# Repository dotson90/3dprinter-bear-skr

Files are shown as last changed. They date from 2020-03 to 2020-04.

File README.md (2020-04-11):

# เครื่องพิมพ์สามมิติ Bear SKR V1
## บทนำ
เครื่องพิมพ์สามมิติ Bear SKR เป็นเครื่องพิมพ์สามมิติสำหรับผู้ที่สนใจสร้างเครื่องพิมพ์สามมิติที่มีโครงสร้างแข็งแรง เชื่อถือได้ ทำให้พิมพ์งานได้เร็วขึ้น มีความแม่นยำสูง และซ่อมบำรุงง่าย
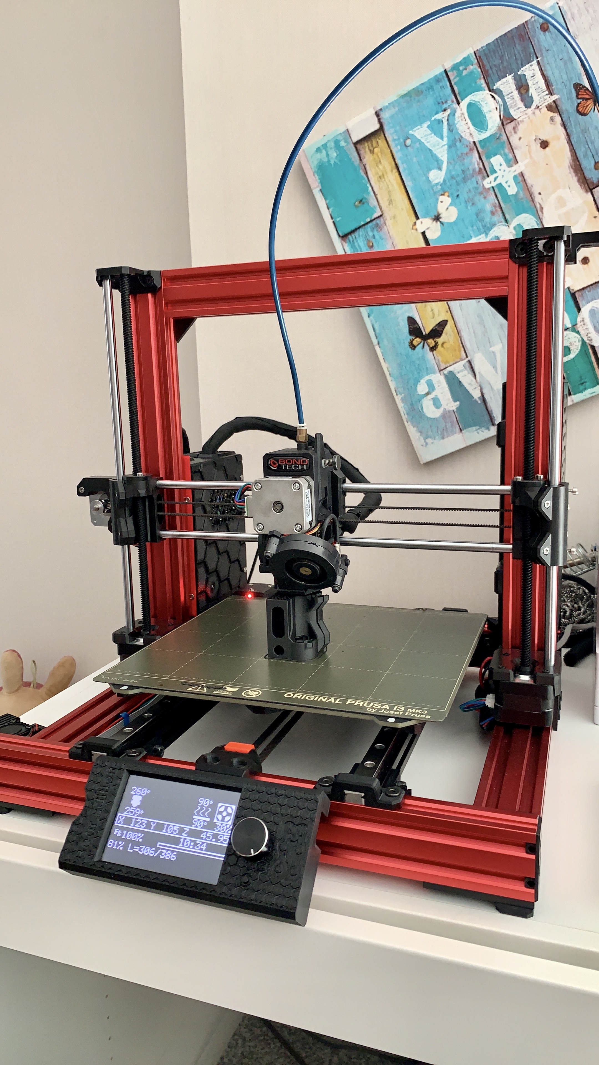
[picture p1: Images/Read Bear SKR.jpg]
Image description


## Todo
* 3D Printed Parts

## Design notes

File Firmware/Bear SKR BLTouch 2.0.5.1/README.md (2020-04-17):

# Bear SKR 2.0.5.1

* บอร์ต BigTreeTech SKR 1.4 Turbo
* BLTouch
* Bondtech BMG
* Stepper 1.8 @ 1A on X, Y, Z and E

### รายการที่แก้ไข

* Restore Flash as the default EEPROM emulation for LPC176x.
* Fix the Z_MIN_PROBE_PIN assignment on SKR 1.4.
* Fix progress bar and M73. (Update your Configuration_adv.h.)
* Fix U.B.L. slot loading.
* Fix Z correction after G29 (ABL Bilinear with Z Fade).
* Fix Z clearance move in G34.
* Fix "remaining time" cosmetic issue

### เปิดใช้ Feature ใหม่

* เปิดใช้งานตั้งฐานพิมพ์อัตโนมัติแบบ UBL

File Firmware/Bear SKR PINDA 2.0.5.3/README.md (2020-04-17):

# Bear SKR 2.0.5.3

### ใช้สำหรับ 

* บอร์ต BigTreeTech SKR 1.4 Turbo
* P.I.N.D.A
* Bondtech BMG
* Stepper 1.8 @ 1A on X, Y, Z and E

### New Features

* Add QSPI EEPROM for SAMD51.
* Case Light brightness stored in EEPROM.

### Issues Patched

* Fix Max7219 delay timing.
* Remove extra call to unskew.
* Formbot T-Rex 2+ default LCD timings.
* Fix M0 unused var warning.
* Fix stepper PWM menu.
* Float pins that can't pull down.
* Fix bad final M2/M3 Arc segment.

### Optimized / Improved

* Simplified SD completion.

### Configuration

* Allow PID_DEBUG to be turned on/off.

### Boards / Pins

* Funmat HT v4.0 board support.
* Fix up Trigorilla 1.4 pins.
* Fix FYSETC STM32 flash usage.
* Fix PINS_DEBUGGING build on STM32F1.

### Hosts and UI

* Update Russian and Italian languages.
* Fix SD finished ExtUI / host action.
* Limited backlash editing with Core kinematics.
* Fix / improve FTDI EVE Touch UI.

### เปิดใช้ Feature ใหม่

* เปิดใช้งานตั้งฐานพิมพ์อัตโนมัติแบบ UBL

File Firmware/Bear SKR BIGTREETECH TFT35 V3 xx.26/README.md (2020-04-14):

# Bear SKR TFT35 V3 xx.26

ใช้สำหรับ หน้าจอ BigTreeTech TFT35 V.3 เท่านั้น

มีการปรับปรุง และแก้ไขปัญหาต่าง ๆ ดังนี้

### เพิ่มเมนู

* เปลี่ยนหัวพิมพ์
* Calibration อัตโนมัติ
* Calibration สำหรับพิมพ์เส้น PLA
* Calibration สำหรับเส้น PETG
* ทำความสะอาดหัวพิมพ์ด้วยวิธีการ Cold Pull อัตโนมัติ
* เปิดให้ Feed เส้นในขนณะที่หัวพิมพ์เย็นได้
* ยกเลิกการ Feed เส้นในขฯะที่หัวพิมพ์เย็น
* Bed Level แบบ UBL อัตโนมัติ พร้อมทั้ง Save เข้า EEPROM Slot 1
* Bed Level แบบ UBL อัตโนมัติ พร้อมทั้ง Save เข้า EEPROM Slot 2
* Bed Level แบบ UBL อัตโนมัติ พร้อมทั้ง Save เข้า EEPROM Slot 3
* ตั้งระยะหัวพิมพ์แบบ UBL ขั้นตอนที่ 1
* ตั้งระยะหัวพิมพ์แบบ UBL ขั้นตอนที่ 2 พร้อมทั้ง Save เข้า EEPROM
* ทำการพิมพ์เพื่อทดสอบ Bed Level
* Adjust Point Near
* ล้าง EEPROM ไปเป็นค่าตั้งต้น

### New Features

* Add LCD backlight control, auto sleep function (Settings->Feature->LCD Brightness)
* Add more Printer setting parameters (Steps/mm, TMC driver current, Feedrate, Acceleration, etc...)
* Add new language(Polish, Slovak, Dutch, Hungarian), up to 15 languages are now supported
* Add support "M300" gcode for TFT buzzer
* Add the TFT with encoder can control the value of menu by encoder
* Add long file name display of onBoardSD(required LONG_FILENAME_HOST_SUPPORT in Marlin)

### Improve

* Improve print menu layout
* Improve Smart Filament Sensor(SFS), (note: required M114_DETAIL and disable LIN_ADVANCE in Marlin, because now LIN_ADVANCE have bugs in Marlin, will be fixed later)
* Improve the tips of "M117" and "echo:" from Marlin
* Improve power loss recovery(PLR), The printing state is saved per layer to reduce the wear of SD card(only support print from TFTSD card now).
* Improve model preview(only support print from TFTSD card now)
* Add more baudrate options on TFT screen

### Bugfix

* Fix error PS_ON_PIN from “PA12” to "PC12" in TFT35_V3.0
* Fix "M104","M109", 'R'/'B'/'F' parameters bug.

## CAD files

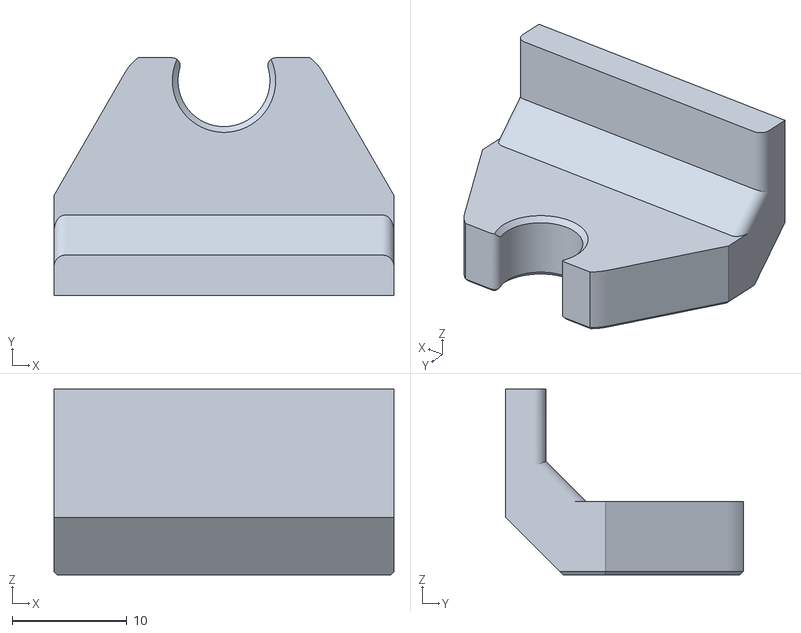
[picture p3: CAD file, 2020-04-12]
Printed Parts/Extruder/Hemera/y_axis_end_stop.stl
29.6 x 20.7 x 16.2

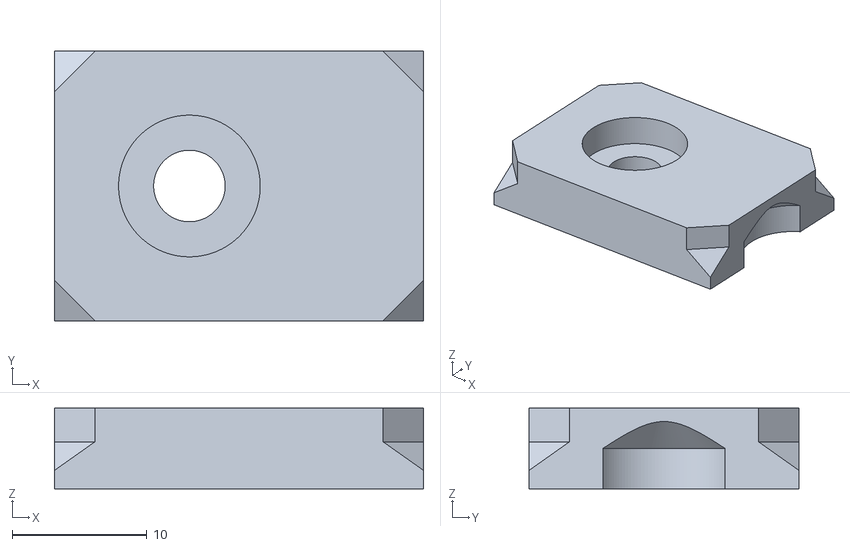
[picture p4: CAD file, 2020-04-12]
Printed Parts/Frame/Stl/foot.stl
27.4 x 20.0 x 6.00

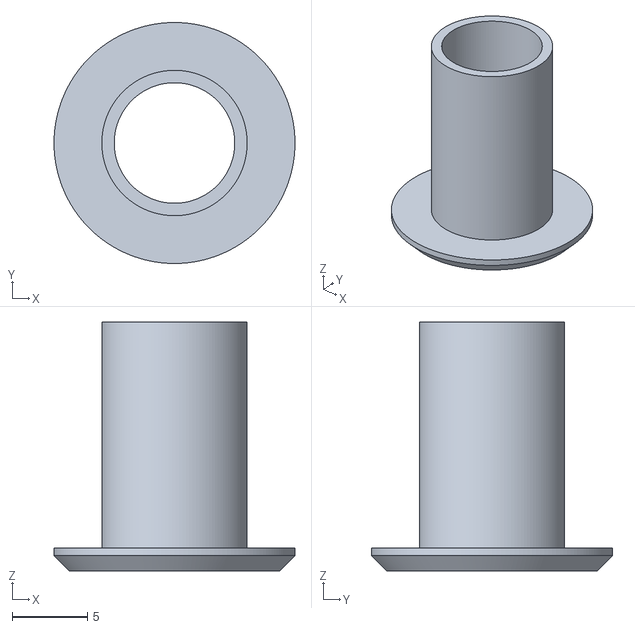
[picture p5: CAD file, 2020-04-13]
Printed Parts/Mean Well LRS-350 PSU Case/voltage_adjust_guide.stl
16.0 x 16.0 x 16.5

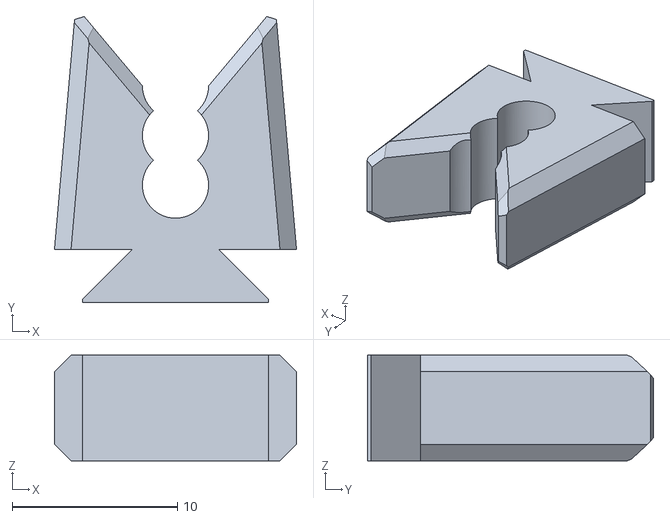
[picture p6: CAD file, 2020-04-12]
Printed Parts/SKR 1.4 Turbo Enclosure/Cable_Holder_Short.stl
14.6 x 17.3 x 6.40

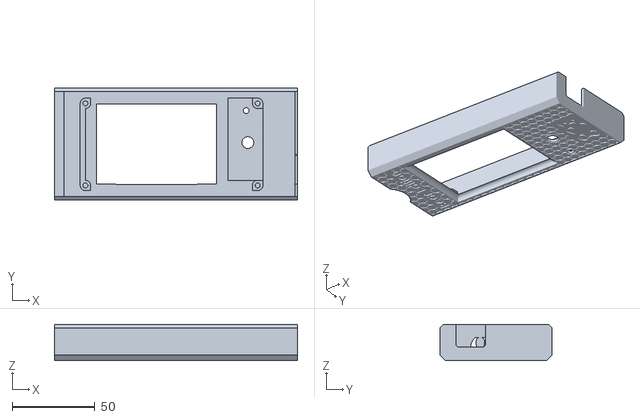
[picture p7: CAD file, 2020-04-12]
Printed Parts/TFT35 Bigtreetech LCD/cover_lcd_skr.stl
146.4 x 67.3 x 21.7

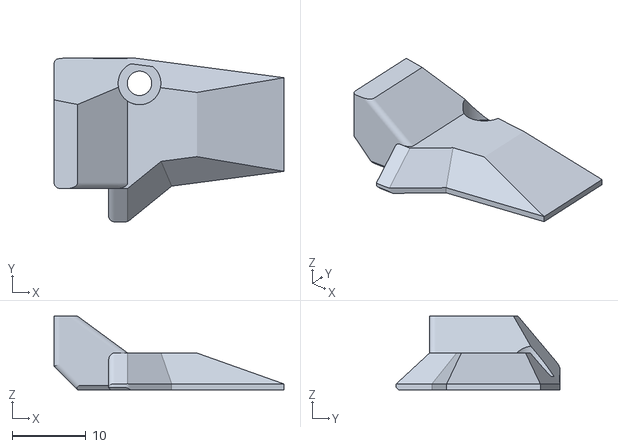
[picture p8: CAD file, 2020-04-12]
Printed Parts/Extruder/Hemera/cable_cover.stl
31.2 x 22.2 x 10.0

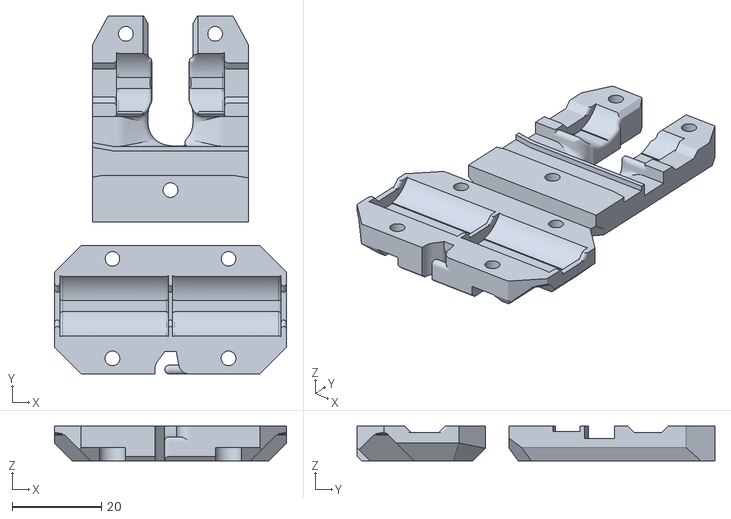
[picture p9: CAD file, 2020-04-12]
Printed Parts/Frame/Stl/x_carriage_back.stl
52.0 x 80.2 x 7.80

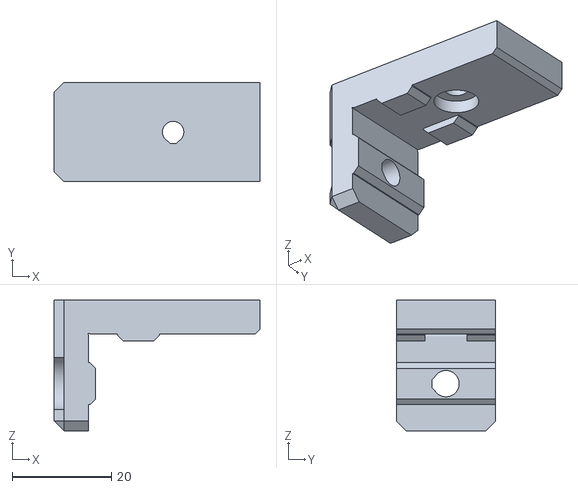
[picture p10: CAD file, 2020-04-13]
Printed Parts/Mean Well LRS-350 PSU Case/psu_upper_mount_mean_well_lrs_350.stl
41.5 x 20.0 x 26.3

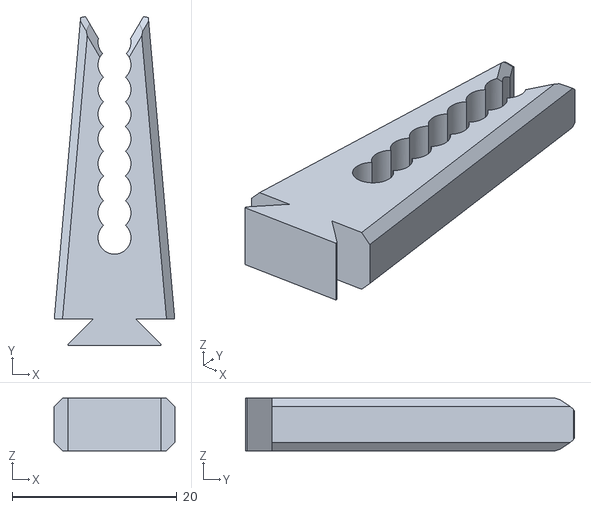
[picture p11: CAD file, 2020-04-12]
Printed Parts/SKR 1.4 Turbo Enclosure/Cable_Holder.stl
14.6 x 40.0 x 6.40

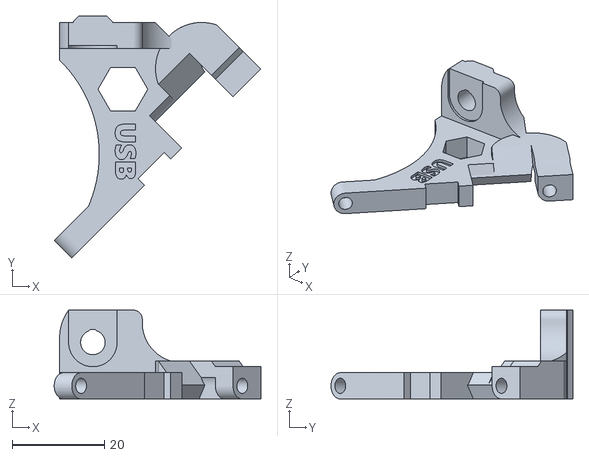
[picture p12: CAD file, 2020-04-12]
Printed Parts/TFT35 Bigtreetech LCD/usb_bracket.stl
44.8 x 52.5 x 19.3

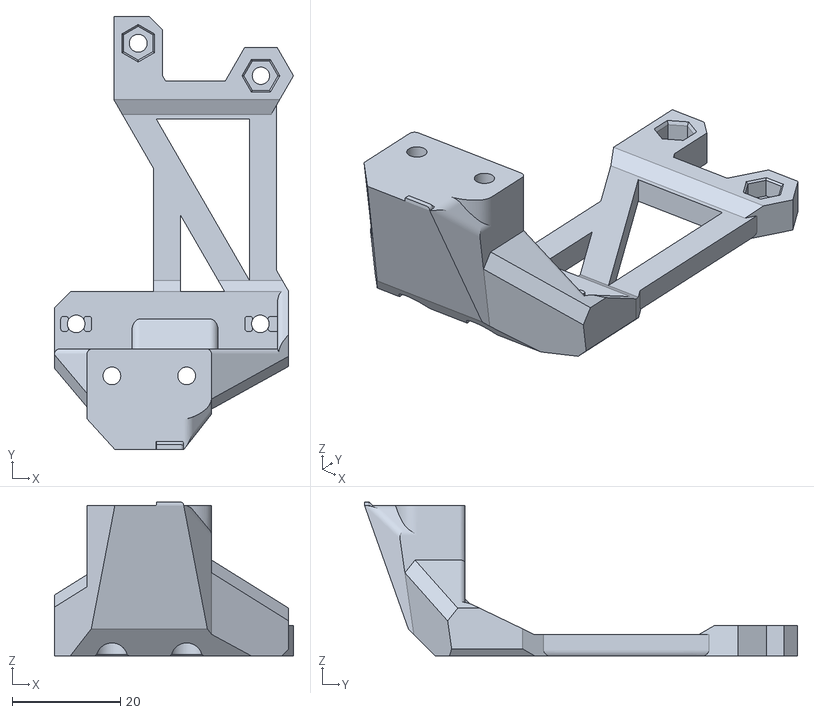
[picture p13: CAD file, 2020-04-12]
Printed Parts/Extruder/Hemera/body_front.stl
44.1 x 80.0 x 28.4

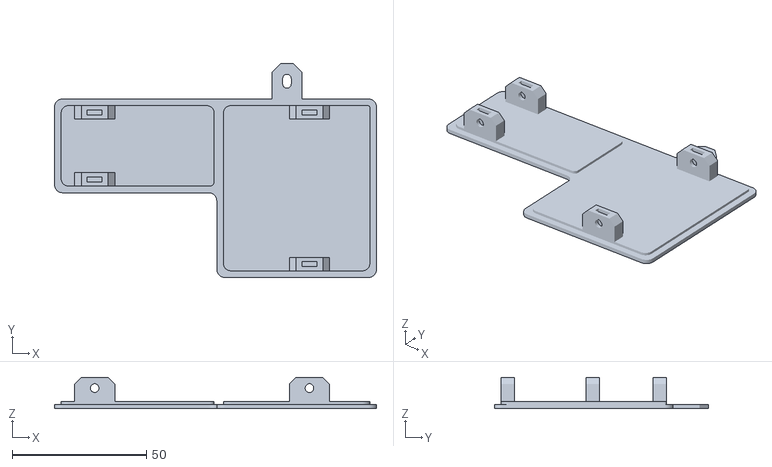
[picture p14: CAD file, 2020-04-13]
Printed Parts/Mean Well LRS-350 PSU Case/bottom.stl
119.9 x 79.7 x 11.6

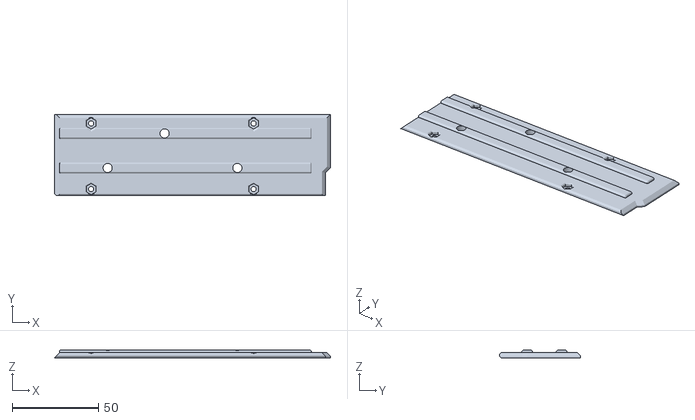
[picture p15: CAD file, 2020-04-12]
Printed Parts/SKR 1.4 Turbo Enclosure/Anchor_SKR_Bear_Short_1.stl
159.7 x 47.0 x 4.40

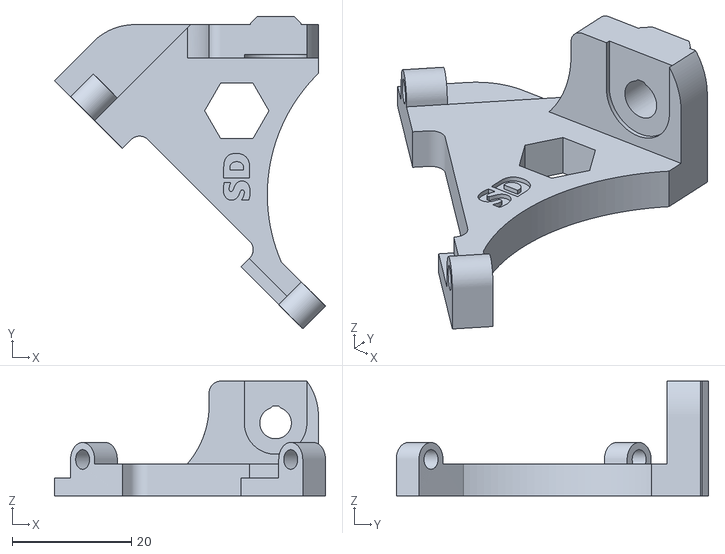
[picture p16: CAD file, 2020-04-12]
Printed Parts/TFT35 Bigtreetech LCD/sd_bracket.stl
45.5 x 52.5 x 19.3

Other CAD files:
Printed Parts/Extruder/Hemera/body_back.stl
Printed Parts/Frame/Stl/y_idler_tensioner_e3d.stl
Printed Parts/Mean Well LRS-350 PSU Case/case.stl
Printed Parts/SKR 1.4 Turbo Enclosure/ESP8266_Cover.stl
Printed Parts/Extruder/Hemera/nozzle_fan_duct.stl
Printed Parts/Extruder/Hemera/nozzle_fan_spacer.stl
Printed Parts/Extruder/Hemera/pinda_mount.stl
Printed Parts/Extruder/Hemera/ptfe_collet_clip.stl
Printed Parts/Extruder/Hemera/x_carriage.stl
Printed Parts/Frame/Stl/bondtech_x_carriage_mk3s.stl
Printed Parts/Frame/Stl/build_helper_y.stl
Printed Parts/Frame/Stl/build_helper_z.stl
Printed Parts/Frame/Stl/cable_clip_lcd.stl
Printed Parts/Frame/Stl/cable_clip_vertical.stl
Printed Parts/Frame/Stl/cable_guide_back_a.stl
Printed Parts/Frame/Stl/cable_guide_back_b.stl
Printed Parts/Frame/Stl/vslot_mount_pc4-m10.stl
Printed Parts/Frame/Stl/x_end_idler.stl
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

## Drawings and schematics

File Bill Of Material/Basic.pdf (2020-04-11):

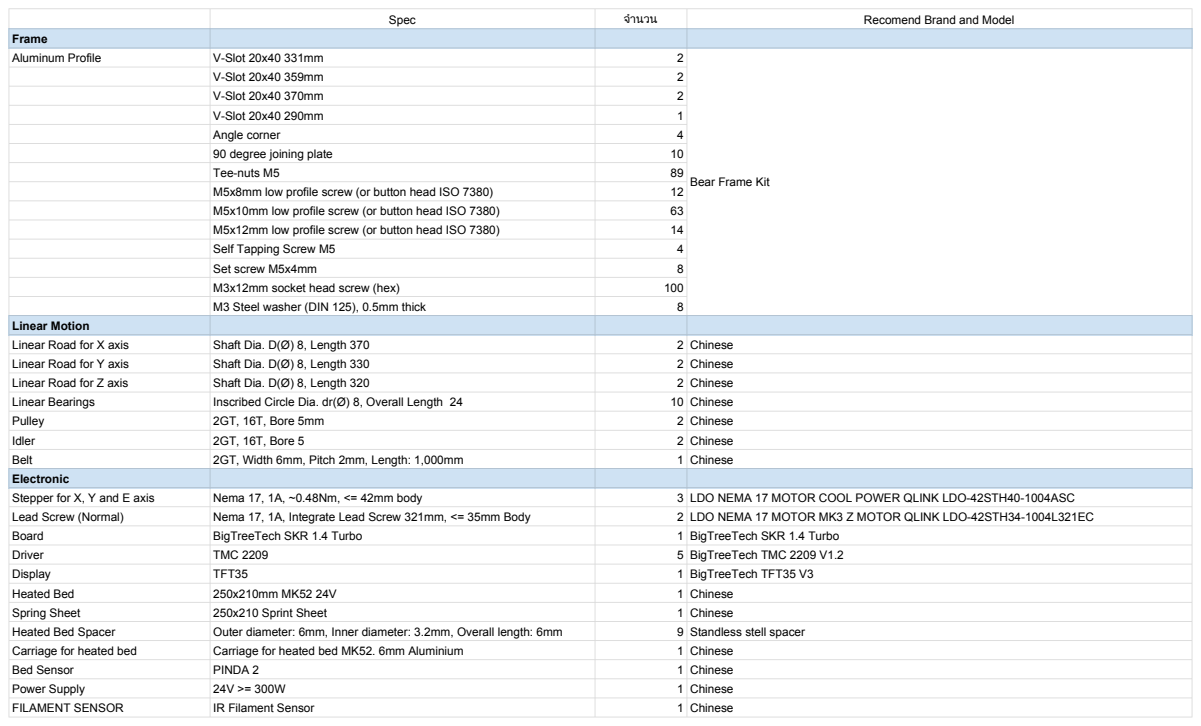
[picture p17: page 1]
Spec; จำนวน; Recomend Brand and Model; Frame; Aluminum Profile; V-Slot 20x40 331mm; V-Slot 20x40 359mm; V-Slot 20x40 370mm; V-Slot 20x40 290mm; Angle corner; 90 degree joining plate; Tee-nuts M5; M5x8mm low profile screw (or button head ISO 7380); M5x10mm low profile screw (or button head ISO 7380); M5x12mm low profile screw (or button head ISO 7380); Self Tapping Screw M5; Set screw M5x4mm; M3x12mm socket head screw (hex); M3 Steel washer (DIN 125), 0.5mm thick; Linear Motion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

Bear Frame Kit

Other | อุปกรณอื่น ๆ เชนสายไฟ ปลั๊ก นอต สกลู M3 | | Chinese หรือ บานหมอ

Extruders
Hotend | E3D V6 | 1 | Clone E3D V6 24V
Drive Gear | BondTech Drivegear KIT 1.75 Inner 5.0 | 1 | Clone BondTech Drivegear KIT 1.75 Inner 5.0
Extruder springs | d = 0.8mm, D = 5.0mm, L = 15.0mm, n = 10, Lm = 8.8mm, Fm = 41.08N | 1 | Original Prusa Extruder Springs
Extruder Fan | 4010 24V | 1 | Chinese
Printed Fan | Radial Cooling Fan 5015 24V | 1 | Chinese

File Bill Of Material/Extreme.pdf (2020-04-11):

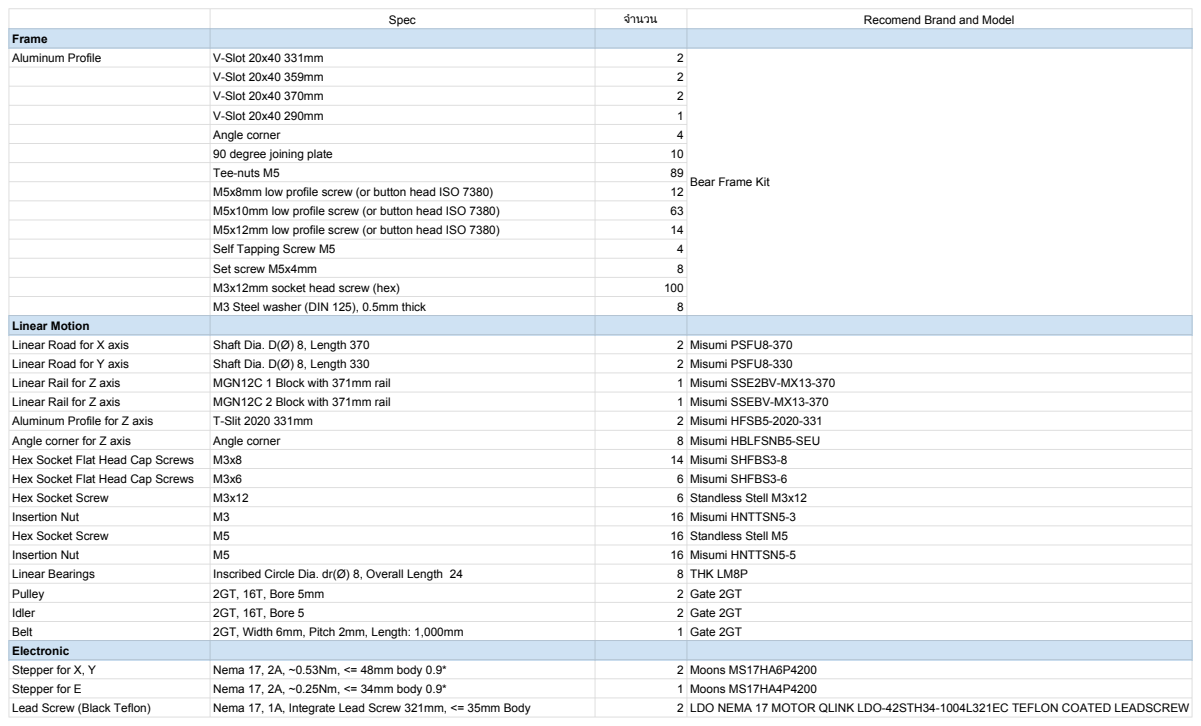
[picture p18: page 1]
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

Bear Frame Kit

Board | BigTreeTech SKR 1.4 Turbo | 1 | BigTreeTech SKR 1.4 Turbo
Driver | TMC 2209 | 5 | BigTreeTech TMC 2209 V1.2
Display | TFT35 | 1 | BigTreeTech TFT35 V3
Heated Bed | MK52 24V | 1 | LDO MK52 24V หรือ Originl Prusa MK52 24V
Heated Bed Spacer | Outer diameter: 6mm, Inner diameter: 3.2mm, Overall length: 6mm | 9 | Standless stell spacer
Carriage for heated bed | Carriage for heated bed MK52. 6mm Aluminium | 1 | Original Prusa Carriage for MK3
Bed Sensor | PINDA 2 | 1 | Original Prusa PINDA 2
Power Supply | 24V >= 300W | 1 | Mean Well LRS-350-24
FILAMENT SENSOR | IR Filament Sensor | 1 | Original Prusa MK3S IR FILAMENT SENSOR
Other | อุปกรณอื่น ๆ เชนสายไฟ ปลั๊ก นอต สกลู M3

Extruders
Hotend | Mosquito Hotend | 1 | Slicer Engineering Mosquito Hotend 24V
Bondtech Extruder upgrade | Prusa I3 MK3S Extruder Mosquito upgrade | 1 | Bondtech Prusa I3 MK3S Extruder Mosquito upgrade
Extruder Fan | 4010 24V | 1 | Mechatronic G4010L24B
Printed Fan | Radial Cooling Fan 5015 24V | 1 | Sanyo Denki 109BC24GC7-1

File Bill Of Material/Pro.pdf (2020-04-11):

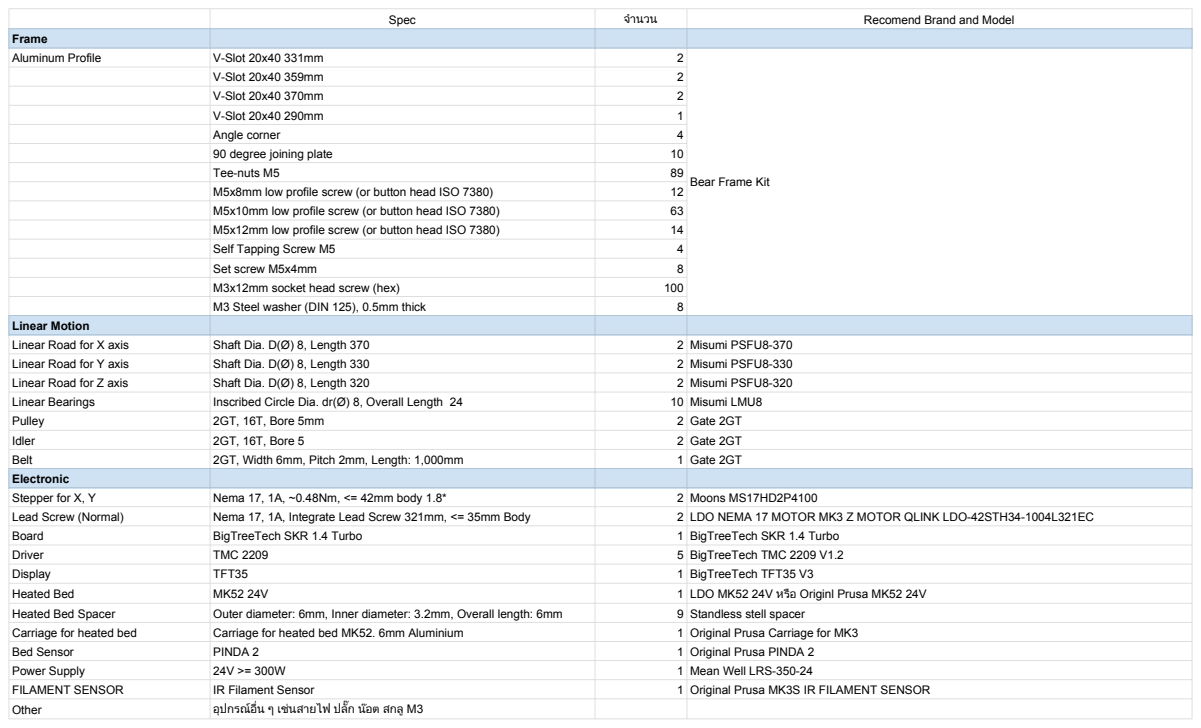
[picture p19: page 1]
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

Bear Frame Kit

Extruders
Hotend | E3D V6 | 1 | E3D V6 24V (Kit)
Bondtech Extruder upgrade | Prusa I3 MK3S Extruder upgrade | 1 | Bondtech Prusa I3 MK3S Extruder upgrade
Extruder Fan | 4010 24V | 1 | SUNON 4010 24V
Printed Fan | Radial Cooling Fan 5015 24V | 1 | SUNON 5015 24V

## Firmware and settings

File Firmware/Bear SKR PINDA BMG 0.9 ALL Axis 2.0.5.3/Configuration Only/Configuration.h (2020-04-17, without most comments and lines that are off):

#pragma once
#define CONFIGURATION_H_VERSION 020005
#define STRING_CONFIG_H_AUTHOR "(Narasak Mansurang, SKR V1.4 Turbo Bear BMG/TMC2209/PINDA)" // Who made the changes.
#define SHOW_BOOTSCREEN
#define SERIAL_PORT 0
#define SERIAL_PORT_2 -1
#define BAUDRATE 115200
  #define MOTHERBOARD BOARD_BTT_SKR_V1_4_TURBO
#define CUSTOM_MACHINE_NAME "Read Bear SKR Turbo"
#define EXTRUDERS 1
#define DEFAULT_NOMINAL_FILAMENT_DIA 1.75
#define TEMP_SENSOR_0 5
#define TEMP_SENSOR_1 0
#define TEMP_SENSOR_2 0
#define TEMP_SENSOR_3 0
#define TEMP_SENSOR_4 0
#define TEMP_SENSOR_5 0
#define TEMP_SENSOR_6 0
#define TEMP_SENSOR_7 0
#define TEMP_SENSOR_BED 1
#define TEMP_SENSOR_PROBE 1
#define TEMP_SENSOR_CHAMBER 0
#define DUMMY_THERMISTOR_998_VALUE 25
#define DUMMY_THERMISTOR_999_VALUE 100
#define MAX_REDUNDANT_TEMP_SENSOR_DIFF 10
#define TEMP_RESIDENCY_TIME     10  // (seconds) Time to wait for hotend to "settle" in M109
#define TEMP_WINDOW              3  // (°C) Temperature proximity for the "temperature reached" timer
#define TEMP_HYSTERESIS          8  // (°C) Temperature proximity considered "close enough" to the target
#define TEMP_BED_RESIDENCY_TIME 10  // (seconds) Time to wait for bed to "settle" in M190
#define TEMP_BED_WINDOW          3  // (°C) Temperature proximity for the "temperature reached" timer
#define TEMP_BED_HYSTERESIS      8  // (°C) Temperature proximity considered "close enough" to the target
#define HEATER_0_MINTEMP   5
#define HEATER_1_MINTEMP   5
#define HEATER_2_MINTEMP   5
#define HEATER_3_MINTEMP   5
#define HEATER_4_MINTEMP   5
#define HEATER_5_MINTEMP   5
#define HEATER_6_MINTEMP   5
#define HEATER_7_MINTEMP   5
#define BED_MINTEMP        5
#define HEATER_0_MAXTEMP 295
#define HEATER_1_MAXTEMP 275
#define HEATER_2_MAXTEMP 275
#define HEATER_3_MAXTEMP 275
#define HEATER_4_MAXTEMP 275
#define HEATER_5_MAXTEMP 275
#define HEATER_6_MAXTEMP 275
#define HEATER_7_MAXTEMP 275
#define BED_MAXTEMP      120
#define PIDTEMP
#define BANG_MAX 255     // Limits current to nozzle while in bang-bang mode; 255=full current
#define PID_MAX BANG_MAX // Limits current to nozzle while PID is active (see PID_FUNCTIONAL_RANGE below); 255=full current
#define PID_K1 0.95      // Smoothing factor within any PID loop
  #define PID_AUTOTUNE_MENU     // Add PID auto-tuning to the "Advanced Settings" menu. (~250 bytes of PROGMEM)
  #define PID_FUNCTIONAL_RANGE 10 // If the temperature difference between the target temperature and the actual temperature
  #define DEFAULT_Kp 16.13
  #define DEFAULT_Ki 1.16
  #define DEFAULT_Kd 56.23
#define PIDTEMPBED
#define MAX_BED_POWER 255 // limits duty cycle to bed; 255=full current
  #define DEFAULT_bedKp 126.13
  #define DEFAULT_bedKi 4.30
  #define DEFAULT_bedKd 924.76
#define PREVENT_COLD_EXTRUSION
#define EXTRUDE_MINTEMP 180
#define PREVENT_LENGTHY_EXTRUDE
#define EXTRUDE_MAXLENGTH 200
#define THERMAL_PROTECTION_HOTENDS // Enable thermal protection for all extruders
#define THERMAL_PROTECTION_BED     // Enable thermal protection for the heated bed
#define THERMAL_PROTECTION_CHAMBER // Enable thermal protection for the heated chamber
#define USE_XMIN_PLUG
#define USE_YMIN_PLUG
#define USE_ZMIN_PLUG
#define ENDSTOPPULLUPS
#define X_MIN_ENDSTOP_INVERTING false // Set to true to invert the logic of the endstop.
#define Y_MIN_ENDSTOP_INVERTING false // Set to true to invert the logic of the endstop.
#define Z_MIN_ENDSTOP_INVERTING false // Set to true to invert the logic of the endstop.
#define X_MAX_ENDSTOP_INVERTING false // Set to true to invert the logic of the endstop.
#define Y_MAX_ENDSTOP_INVERTING false // Set to true to invert the logic of the endstop.
#define Z_MAX_ENDSTOP_INVERTING false // Set to true to invert the logic of the endstop.
#define Z_MIN_PROBE_ENDSTOP_INVERTING false // Set to true to invert the logic of the probe.
#define X_DRIVER_TYPE  TMC2209
#define Y_DRIVER_TYPE  TMC2209
#define Z_DRIVER_TYPE  TMC2209
#define Z2_DRIVER_TYPE TMC2209
#define E0_DRIVER_TYPE TMC2209
#define DEFAULT_AXIS_STEPS_PER_UNIT   { 400, 400, 400, 1660 }
#define DEFAULT_MAX_FEEDRATE          { 200, 200, 30, 120 }
#define DEFAULT_MAX_ACCELERATION      { 1250, 1250, 200, 10000 }
#define DEFAULT_ACCELERATION          1250    // X, Y, Z and E acceleration for printing moves
#define DEFAULT_RETRACT_ACCELERATION  1250    // E acceleration for retracts
#define DEFAULT_TRAVEL_ACCELERATION   1250   // X, Y, Z acceleration for travel (non printing) moves
#define DEFAULT_EJERK    3.5  // May be used by Linear Advance
  #define JUNCTION_DEVIATION_MM 0.017 // (mm) Distance from real junction edge
#define S_CURVE_ACCELERATION
#define Z_MIN_PROBE_USES_Z_MIN_ENDSTOP_PIN
#define FIX_MOUNTED_PROBE
#define NOZZLE_TO_PROBE_OFFSET { 23, 5, 0 }
#define MIN_PROBE_EDGE 10
#define XY_PROBE_SPEED 8000
#define Z_PROBE_SPEED_FAST (HOMING_FEEDRATE_Z * 4)
#define Z_PROBE_SPEED_SLOW (Z_PROBE_SPEED_FAST / 2)
#define MULTIPLE_PROBING 3
#define Z_CLEARANCE_DEPLOY_PROBE    2 // Z Clearance for Deploy/Stow
#define Z_CLEARANCE_BETWEEN_PROBES  2 // Z Clearance between probe points
#define Z_CLEARANCE_MULTI_PROBE     2 // Z Clearance between multiple probes
#define Z_PROBE_LOW_POINT          -2 // Farthest distance below the trigger-point to go before stopping
#define Z_PROBE_OFFSET_RANGE_MIN -20
#define Z_PROBE_OFFSET_RANGE_MAX 20
#define Z_MIN_PROBE_REPEATABILITY_TEST
#define X_ENABLE_ON 0
#define Y_ENABLE_ON 0
#define Z_ENABLE_ON 0
#define E_ENABLE_ON 0 // For all extruders
#define DISABLE_X false
#define DISABLE_Y false
#define DISABLE_Z false
#define DISABLE_E false             // For all extruders
#define DISABLE_INACTIVE_EXTRUDER   // Keep only the active extruder enabled
#define INVERT_X_DIR false
#define INVERT_Y_DIR true
#define INVERT_Z_DIR false
#define INVERT_E0_DIR false
#define INVERT_E1_DIR false
#define INVERT_E2_DIR false
#define INVERT_E3_DIR false
#define INVERT_E4_DIR false
#define INVERT_E5_DIR false
#define INVERT_E6_DIR false
#define INVERT_E7_DIR false
#define X_HOME_DIR -1
#define Y_HOME_DIR -1
#define Z_HOME_DIR -1
#define X_BED_SIZE 250
#define Y_BED_SIZE 212.5
#define X_MIN_POS 0
#define Y_MIN_POS -4
#define Z_MIN_POS 0
#define X_MAX_POS X_BED_SIZE
#define Y_MAX_POS Y_BED_SIZE
#define Z_MAX_POS 210
#define MIN_SOFTWARE_ENDSTOPS
  #define MIN_SOFTWARE_ENDSTOP_X
  #define MIN_SOFTWARE_ENDSTOP_Y
  #define MIN_SOFTWARE_ENDSTOP_Z
#define MAX_SOFTWARE_ENDSTOPS
  #define MAX_SOFTWARE_ENDSTOP_X
  #define MAX_SOFTWARE_ENDSTOP_Y
  #define MAX_SOFTWARE_ENDSTOP_Z
  #define SOFT_ENDSTOPS_MENU_ITEM  // Enable/Disable software endstops from the LCD
#define FILAMENT_RUNOUT_SENSOR
  #define NUM_RUNOUT_SENSORS   1     // Number of sensors, up to one per extruder. Define a FIL_RUNOUT#_PIN for each.
  #define FIL_RUNOUT_INVERTING true // Set to true to invert the logic of the sensor.
  #define FIL_RUNOUT_PULLUP          // Use internal pullup for filament runout pins.
  #define FILAMENT_RUNOUT_SCRIPT "M600"
  #define FILAMENT_RUNOUT_DISTANCE_MM 2
#define AUTO_BED_LEVELING_UBL
#define RESTORE_LEVELING_AFTER_G28
  #define ENABLE_LEVELING_FADE_HEIGHT
  #define SEGMENT_LEVELED_MOVES
  #define LEVELED_SEGMENT_LENGTH 5.0 // (mm) Length of all segments (except the last one)
  #define G26_MESH_VALIDATION
    #define MESH_TEST_NOZZLE_SIZE    0.4  // (mm) Diameter of primary nozzle.
    #define MESH_TEST_LAYER_HEIGHT   0.2  // (mm) Default layer height for the G26 Mesh Validation Tool.
    #define MESH_TEST_HOTEND_TEMP  210    // (°C) Default nozzle temperature for the G26 Mesh Validation Tool.
    #define MESH_TEST_BED_TEMP      60    // (°C) Default bed temperature for the G26 Mesh Validation Tool.
    #define G26_XY_FEEDRATE         20    // (mm/s) Feedrate for XY Moves for the G26 Mesh Validation Tool.
    #define G26_RETRACT_MULTIPLIER   1.0  // G26 Q (retraction) used by default between mesh test elements.
  #define MESH_INSET 1              // Set Mesh bounds as an inset region of the bed
  #define GRID_MAX_POINTS_X 10       // Don't use more than 15 points per axis, implementation limited.
  #define GRID_MAX_POINTS_Y GRID_MAX_POINTS_X
  #define UBL_MESH_EDIT_MOVES_Z     // Sophisticated users prefer no movement of nozzle
  #define UBL_SAVE_ACTIVE_ON_M500   // Save the currently active mesh in the current slot on M500
  #define UBL_Z_RAISE_WHEN_OFF_MESH 0 // When the nozzle is off the mesh, this value is used
#define MANUAL_X_HOME_POS 0
#define MANUAL_Y_HOME_POS -3
#define MANUAL_Z_HOME_POS 0.2
#define Z_SAFE_HOMING
  #define Z_SAFE_HOMING_X_POINT ((X_BED_SIZE) / 2)    // X point for Z homing when homing all axes (G28).
  #define Z_SAFE_HOMING_Y_POINT ((Y_BED_SIZE) / 2)    // Y point for Z homing when homing all axes (G28).
#define HOMING_FEEDRATE_XY (50*60)
#define HOMING_FEEDRATE_Z  (4*60)
#define VALIDATE_HOMING_ENDSTOPS
#define EEPROM_SETTINGS     // Persistent storage with M500 and M501
#define EEPROM_CHITCHAT       // Give feedback on EEPROM commands. Disable to save PROGMEM.
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

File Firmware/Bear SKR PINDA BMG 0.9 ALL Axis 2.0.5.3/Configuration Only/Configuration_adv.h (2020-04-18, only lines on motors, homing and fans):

#define E0_AUTO_FAN_PIN P2_04
#define E1_AUTO_FAN_PIN -1
#define E2_AUTO_FAN_PIN -1
#define E3_AUTO_FAN_PIN -1
#define E4_AUTO_FAN_PIN -1
#define E5_AUTO_FAN_PIN -1
#define CHAMBER_AUTO_FAN_PIN -1
#define X_HOME_BUMP_MM 0
#define Y_HOME_BUMP_MM 0
#define Z_HOME_BUMP_MM 0
#define HOMING_BUMP_DIVISOR { 2, 2, 4 }  // Re-Bump Speed Divisor (Divides the Homing Feedrate)
#define HOMING_BACKOFF_MM { 2, 2, 2 }  // (mm) Move away from the endstops after homing
  #define HOME_AFTER_G34
#define MICROSTEP_MODES { 16, 16, 16, 16, 16, 16 } // [1,2,4,8,16]
#define DIGIPOT_I2C_MOTOR_CURRENTS { 1.0, 1.0, 1.0, 1.0, 1.0, 1.0, 1.0, 1.0 }  //  AZTEEG_X3_PRO
#define LIN_ADVANCE
  #define LIN_ADVANCE_K 0.00    // Unit: mm compression per 1mm/s extruder speed
#define ADVANCED_PAUSE_FEATURE
  #define ADVANCED_PAUSE_PURGE_FEEDRATE        3  // (mm/s) Extrude feedrate (after loading). Should be slower than load feedrate.
  #define ADVANCED_PAUSE_PURGE_LENGTH         60  // (mm) Length to extrude after loading.
  #define ADVANCED_PAUSE_RESUME_PRIME          0  // (mm) Extra distance to prime nozzle after returning from park.
    #define X_CURRENT       1400        // (mA) RMS current. Multiply by 1.414 for peak current.
    #define X_CURRENT_HOME  300  // (mA) RMS current for sensorless homing
    #define X_MICROSTEPS     32    // 0..256
    #define Y_CURRENT       1400
    #define Y_CURRENT_HOME  400
    #define Y_MICROSTEPS     32
    #define Z_CURRENT       450
    #define Z_CURRENT_HOME  Z_CURRENT
    #define Z_MICROSTEPS     16
    #define Z2_CURRENT      450
    #define Z2_CURRENT_HOME Z2_CURRENT
    #define Z2_MICROSTEPS    16
    #define E0_CURRENT      1400
    #define E0_MICROSTEPS    32
    #define CURRENT_STEP_DOWN     50  // [mA]
    #define REPORT_CURRENT_CHANGE
  #define X_HYBRID_THRESHOLD     100  // [mm/s]
  #define X2_HYBRID_THRESHOLD    100
  #define Y_HYBRID_THRESHOLD     100
  #define Y2_HYBRID_THRESHOLD    100
  #define Z_HYBRID_THRESHOLD       3
  #define Z2_HYBRID_THRESHOLD      3
  #define Z3_HYBRID_THRESHOLD      3
  #define Z4_HYBRID_THRESHOLD      3
  #define E0_HYBRID_THRESHOLD     30
  #define E1_HYBRID_THRESHOLD     30
  #define E2_HYBRID_THRESHOLD     30
  #define E3_HYBRID_THRESHOLD     30
  #define E4_HYBRID_THRESHOLD     30
  #define E5_HYBRID_THRESHOLD     30
  #define E6_HYBRID_THRESHOLD     30
  #define E7_HYBRID_THRESHOLD     30
  #define SENSORLESS_HOMING // StallGuard capable drivers only
    #define X_STALL_SENSITIVITY  81
    #define X2_STALL_SENSITIVITY X_STALL_SENSITIVITY
    #define Y_STALL_SENSITIVITY  85
    #define IMPROVE_HOMING_RELIABILITY

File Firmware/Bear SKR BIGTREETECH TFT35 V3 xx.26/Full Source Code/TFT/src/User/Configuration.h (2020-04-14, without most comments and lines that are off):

#define _CONFIGRATION_H_
#define DEFAULT_LCD_MODE SERIAL_TSC
#define STARTUP_KNOB_LED_COLOR 1         // LED_OFF
#define KEEP_KNOB_LED_COLOR_MARLIN_MODE  // Keeps the LED state in Marlin Mode
#define DEFAULT_LCD_BRIGHTNESS      11  // 11: LCD_100_PERCENT - Brightness value from list
#define DEFAULT_LCD_IDLE_BRIGHTNESS 2   // 2: LCD_10_PERCENT - Brightness value from list
#define DEFAULT_LCD_IDLE_TIMER      1   // 1: LCD_DIM_OFF
#define LCD_DIM_CUSTOM_SECONDS      600 // Custom value in seconds. Will be used if
#define ST7920_BKCOLOR BLACK
#define ST7920_FNCOLOR YELLOW
#define DEFAULT_ST7920_FULLSCREEN_MODE 0 // 0: Disabled. RECOMMENDED FOR TFT24
#define BAUDRATE 115200
#define DEFAULT_LANGUAGE ENGLISH
#define SHOW_BTT_BOOTSCREEN
#define BUZZER_FREQUENCY_DURATION_MS 20 // Default 20
#define BUZZER_FREQUENCY_HZ 10000       // Default 10000, 20Hz to 60KHz
#define BUZZER_STOP_LEVEL false
#define TITLE_BACKGROUND_COLOR      BLACK  // Title background color // 0xD928
#define BACKGROUND_COLOR            BLACK  // Background color // 0x0A29
#define FONT_COLOR                  WHITE  // Font foreground color
#define REMINDER_FONT_COLOR         RED    // Reminder font color, such as: "No print attached", "Busy processing", etc.
#define VOLUME_REMINDER_FONT_COLOR  GBLUE  // Volume reminder font color, such as: "Card inserted", "Card removed"
#define TOOL_NUM     1    // set in 1~6
#define EXTRUDER_NUM 1    // set in 1~6
#define FAN_NUM      1    // set in 1~6
#define PREHEAT_BED      {60,      70,       100}
#define PREHEAT_HOTEND   {200,     250,      250}
#define HEAT_MAX_TEMP    {120,    295,       275,       275,       275,       275,       275}    //max temperature can be set
#define HEAT_SIGN_ID     {"B:",   "T0:",     "T1:",     "T2:",     "T3:",     "T4:",     "T5:"}
#define HEAT_DISPLAY_ID  {"Bed",  "T0",      "T1",      "T2",      "T3",      "T4",      "T5"}
#define HEAT_CMD         {"M140", "M104 T0", "M104 T1", "M104 T2", "M104 T3", "M104 T4", "M104 T5" };
#define HEAT_WAIT_CMD    {"M190", "M109 T0", "M109 T1", "M109 T2", "M109 T3", "M109 T4", "M109 T5" };
#define TOOL_CHANGE      {"T0",   "T1",      "T2",      "T3",      "T4",      "T5"}
#define EXTRUDER_ID      {"E0",   "E1",      "E2",      "E3",      "E4",      "E5"}
#define FAN_MAX_PWM      {255,       255,       255,       255,       255,       255}
#define FAN_ID           {"F0",    "F1",    "F2",    "F3",    "F4",    "F5"}
#define FAN_CMD          {"M106 P0", "M106 P1", "M106 P2", "M106 P3", "M106 P4", "M106 P5" };
#define SPEED_ID         {"Sp.", "Fr."}
#define AXIS_DISPLAY_ID  {"X",  "Y",  "Z",   "E",  "E2"}
#define DEFAULT_SPEED_MOVE      3000
#define SPEED_MOVE_SLOW         1000
#define SPEED_MOVE_FAST         5000
#define EXTRUDE_SLOW_SPEED      60
#define EXTRUDE_NORMAL_SPEED    600
#define EXTRUDE_FAST_SPEED      1200
#define X_MIN_POS 0
#define Y_MIN_POS -4
#define Z_MIN_POS 0
#define X_MAX_POS 250
#define Y_MAX_POS 212.5
#define Z_MAX_POS 210
#define NOZZLE_PAUSE_RETRACT_LENGTH 15   // (mm)
#define NOZZLE_RESUME_PURGE_LENGTH  16   // (mm)
#define NOZZLE_PAUSE_X_POSITION     (X_MIN_POS + 10)  // (mm) Must be an integer
#define NOZZLE_PAUSE_Y_POSITION     (Y_MIN_POS + 10)  // (mm) Must be an integer
#define NOZZLE_PAUSE_Z_RAISE        20   // (mm)
#define NOZZLE_PAUSE_E_FEEDRATE     6000 // (mm/min) retract & purge feedrate
#define NOZZLE_PAUSE_XY_FEEDRATE    6000 // (mm/min) X and Y axes feedrate
#define NOZZLE_PAUSE_Z_FEEDRATE     300  // (mm/min) Z axis feedrate
#define AUTO_SAVE_LOAD_LEVELING_VALUE
#define LEVELING_POINT_1_X         (X_MIN_POS + 20)
#define LEVELING_POINT_1_Y         (Y_MIN_POS + 20)
#define LEVELING_POINT_2_X         (X_MAX_POS - 20)
#define LEVELING_POINT_2_Y         (Y_MIN_POS + 20)
#define LEVELING_POINT_3_X         (X_MAX_POS - 20)
#define LEVELING_POINT_3_Y         (Y_MAX_POS - 20)
#define LEVELING_POINT_4_X         (X_MIN_POS + 20)
#define LEVELING_POINT_4_Y         (Y_MAX_POS - 20)
#define LEVELING_POINT_Z           0.2f  // Z-axis position when nozzle stays for leveling
#define LEVELING_POINT_MOVE_Z      10.0f // Z-axis position when nozzle move to next point
#define LEVELING_POINT_XY_FEEDRATE 6000  // (mm/min) X and Y axes move feedrate
#define LEVELING_POINT_Z_FEEDRATE  600   // (mm/min) Z axis move feedrate
#define PS_ON_ACTIVE_HIGH    true   // Set 'false' for ATX (1), 'true' for X-Box (2)
#define FIL_RUNOUT_INVERTING true  // Set to false to invert the logic of the sensor.
#define FIL_NOISE_THRESHOLD  100   // 100ms,  Pause print when filament runout is detected for 100ms.
#define FILAMENT_RUNOUT_DISTANCE_MM 7
#define ALTERNATIVE_MOVE_MENU
#define UNIFIED_MENU
#define ONBOARD_SD_SUPPORT
  #define M27_REFRESH                3        // Time in sec for M27 command
  #define M27_WATCH_OTHER_SOURCES    true     // if true the polling on M27 report is always active. Case: SD print started not from TFT35
#define POWER_LOSS_ZRAISE 10 // (mm) Raise Z axis on resume (on power loss with UPS)
#define PREVENT_COLD_EXTRUSION_MINTEMP 170
#define AUTO_SHUT_DOWN_MAXTEMP 50
#define SHOW_FAN_PERCENTAGE // enable to show fan speed as a percentage instead of a value
#define RAPID_SERIAL_COMM
#define CUSTOM_0_LABEL "Nozzle Change"
#define CUSTOM_0_GCODE "M104 S275\nM117 Setting Nozzle to 275C\nG4 s3\nM0 Click to continue"
#define CUSTOM_1_LABEL "Full Calibration"
#define CUSTOM_1_GCODE "M140 S60\nM190 S60\nG28\nG34\nG29\nM500\nM140 S0\nG28"
#define CUSTOM_2_LABEL "PLA Z Calibration"
#define CUSTOM_2_GCODE "G28\nM107\nM140 S60\nM190 S60\nM104 S160\nM109 S160\nG29 L1\nG1 X2.0 Y-2.0 Z0.60\nM104 S205\nM109 S205\nM0 Click to continue\nG92 E0.00\nG1 Z0.2 X60 E9.0 F1000.0\nG1 X100.0 E12.5 F1000.0\nG92 E0.0\nG21\nG90\nM83\nG1 E-1.50000 F2100.00000\nG1 Z0.150 F7200.000\nM204 S1000\nG1 F4000\nG1 X50 Y155\nG1 F1080\nG1 X75 Y155 E2.5\nG1 X100 Y155 E2\nG1 X200 Y155 E2.62773\nG1 X200 Y135 E0.66174\nG1 X50 Y135 E3.62773\nG1 X50 Y115 E0.49386\nG1 X200 Y115 E3.62773\nG1 X200 Y95 E0.49386\nG1 X50 Y95 E3.62773\nG1 X50 Y75 E0.49386\nG1 X200 Y75 E3.62773\nG1 X200 Y55 E0.49386\nG1 X50 Y55 E3.62773\nG1 X50 Y35 E0.49386\nG1 X70 Y35 E0.49386\nG1 X70 Y34.6 E0\nG1 X50 Y34.6 E0.49386\nG1 X50 Y34.2 E0\nG1 X70 Y34.2 E0.49386\nG1 X70 Y33.8 E0\nG1 X50 Y33.8 E0.49386\nG1 X50 Y33.4 E0\nG1 X70 Y33.4 E0.49386\nG1 X70 Y33.0 E0\nG1 X50 Y33.0 E0.49386\nG1 X50 Y32.6 E0\nG1 X70 Y32.6 E0.49386\nG1 X70 Y32.2 E0\nG1 X50 Y32.2 E0.49386\nG1 X50 Y31.8 E0\nG1 X70 Y31.8 E0.49386\nG1 X70 Y31.4 E0\nG1 X50 Y31.4 E0.49386\nG1 X50 Y31.0 E0\nG1 X70 Y31.0 E0.49386\nG1 X70 Y30.6 E0\nG1 X50 Y30.6 E0.49386\nG1 X50 Y30.2 E0\nG1 X70 Y30.2 E0.49386\nG1 X70 Y29.8 E0\nG1 X50 Y29.8 E0.49386\nG1 X50 Y29.4 E0\nG1 X70 Y29.4 E0.49386\nG1 X70 Y29.0 E0\nG1 X50 Y29.0 E0.49386\nG1 X50 Y28.6 E0\nG1 X70 Y28.6 E0.49386\nG1 X70 Y28.2 E0\nG1 X50 Y28.2 E0.49386\nG1 X50 Y27.8 E0\nG1 X70 Y27.8 E0.49386\nG1 X70 Y27.4 E0\nG1 X50 Y27.4 E0.49386\nG1 X50 Y27.0 E0\nG1 X70 Y27.0 E0.49386\nG1 X70 Y26.6 E0\nG1 X50 Y26.6 E0.49386\nG1 X50 Y26.2 E0\nG1 X70 Y26.2 E0.49386\nG1 X70 Y25.8 E0\nG1 X50 Y25.8 E0.49386\nG1 X50 Y25.4 E0\nG1 X70 Y25.4 E0.49386\nG1 X70 Y25.0 E0\nG1 X50 Y25.0 E0.49386\nG1 X50 Y24.6 E0\nG1 X70 Y24.6 E0.49386\nG1 X70 Y24.2 E0\nG1 X50 Y24.2 E0.49386\nG1 X50 Y23.8 E0\nG1 X70 Y23.8 E0.49386\nG1 X70 Y23.4 E0\nG1 X50 Y23.4 E0.49386\nG1 X50 Y23.0 E0\nG1 X70 Y23.0 E0.49386\nG1 X70 Y22.6 E0\nG1 X50 Y22.6 E0.49386\nG1 X50 Y22.2 E0\nG1 X70 Y22.2 E0.49386\nG1 X70 Y21.8 E0\nG1 X50 Y21.8 E0.49386\nG1 X50 Y21.4 E0\nG1 X70 Y21.4 E0.49386\nG1 X70 Y21.0 E0\nG1 X50 Y21.0 E0.49386\nG1 X50 Y20.6 E0\nG1 X70 Y20.6 E0.49386\nG1 X70 Y20.2 E0\nG1 X50 Y20.2 E0.49386\nG1 X50 Y19.8 E0\nG1 X70 Y19.8 E0.49386\nG1 X70 Y19.4 E0\nG1 X50 Y19.4 E0.49386\nG1 E-0.07500 F2100.00000\nG4\nM107\nM104 S0\nM140 S0\nG1 X10 Y180 F4000\nG1 Z10 F1300.000\nM500\nM0 Happy Printing\nM84"
#define CUSTOM_3_LABEL "PETG Z Calibration"
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

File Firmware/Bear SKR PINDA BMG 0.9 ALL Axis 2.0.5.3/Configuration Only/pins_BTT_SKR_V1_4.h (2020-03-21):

/**
 * Marlin 3D Printer Firmware
 * Copyright (c) 2020 MarlinFirmware [https://github.com/MarlinFirmware/Marlin]
 *
 * Based on Sprinter and grbl.
 * Copyright (c) 2011 Camiel Gubbels / Erik van der Zalm
 *
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
 */
#pragma once

#ifndef BOARD_INFO_NAME
  #define BOARD_INFO_NAME "BIGTREE SKR 1.4"
#endif

//
// EEPROM
//
#if NONE(FLASH_EEPROM_EMULATION, SDCARD_EEPROM_EMULATION)
  #define FLASH_EEPROM_EMULATION
  //#define SDCARD_EEPROM_EMULATION
#endif

//
// SD Connection
//
#ifndef SDCARD_CONNECTION
  #define SDCARD_CONNECTION LCD
#endif

//
// Servos
//
#define SERVO0_PIN         P2_00

//
// TMC StallGuard DIAG pins
//
#define X_DIAG_PIN         P1_29   // X-STOP
#define Y_DIAG_PIN         P1_28   // Y-STOP
#define Z_DIAG_PIN         P1_27   // Z-STOP
#define E0_DIAG_PIN        P1_26   // E0DET
#define E1_DIAG_PIN        P1_25   // E1DET

//
// Limit Switches
//
#if X_STALL_SENSITIVITY
  #define X_STOP_PIN       X_DIAG_PIN
  #if X_HOME_DIR < 0
    #define X_MAX_PIN      P1_26   // E0DET
  #else
    #define X_MIN_PIN      P1_26   // E0DET
  #endif
#else
  #define X_STOP_PIN       P1_29   // X-STOP
#endif

#if Y_STALL_SENSITIVITY
  #define Y_STOP_PIN       Y_DIAG_PIN
  #if Y_HOME_DIR < 0
    #define Y_MAX_PIN      P1_25   // E1DET
  #else
    #define Y_MIN_PIN      P1_25   // E1DET
  #endif
#else
  #define Y_STOP_PIN       P1_28   // Y-STOP
#endif

#if Z_STALL_SENSITIVITY
  #define Z_STOP_PIN       Z_DIAG_PIN
  #if Z_HOME_DIR < 0
    #define Z_MAX_PIN      P1_00   // PWRDET
  #else
    #define Z_MIN_PIN      P1_00   // PWRDET
  #endif
#else
  #ifndef Z_STOP_PIN
    #define Z_STOP_PIN     P0_10   // Z-STOP
  #endif
#endif

//
// Z Probe (when not Z_MIN_PIN)
//
#ifndef Z_MIN_PROBE_PIN
  #define Z_MIN_PROBE_PIN  P0_10
#endif

//
// Filament Runout Sensor
//
#define FIL_RUNOUT_PIN     P1_26   // E0DET
#define FIL_RUNOUT2_PIN    P1_25   // E1DET

//
// Power Supply Control
//
#ifndef PS_ON_PIN
  #define PS_ON_PIN        P1_00   // PWRDET
#endif

//
// Power Loss Detection
//
#ifndef POWER_LOSS_PIN
  #define POWER_LOSS_PIN   P1_00   // PWRDET
#endif

//
// Steppers
//
#define X_STEP_PIN         P2_02
#define X_DIR_PIN          P2_06
#define X_ENABLE_PIN       P2_01
#ifndef X_CS_PIN
  #define X_CS_PIN         P1_10
#endif

#define Y_STEP_PIN         P0_19
#define Y_DIR_PIN          P0_20
#define Y_ENABLE_PIN       P2_08
#ifndef Y_CS_PIN
  #define Y_CS_PIN         P1_09
#endif

#define Z_STEP_PIN         P0_22
#define Z_DIR_PIN          P2_11
#define Z_ENABLE_PIN       P0_21
#ifndef Z_CS_PIN
  #define Z_CS_PIN         P1_08
#endif

#define E0_STEP_PIN        P2_13
#define E0_DIR_PIN         P0_11
#define E0_ENABLE_PIN      P2_12
#ifndef E0_CS_PIN
  #define E0_CS_PIN        P1_04
#endif

#define E1_STEP_PIN        P1_15
#define E1_DIR_PIN         P1_14
#define E1_ENABLE_PIN      P1_16
#ifndef E1_CS_PIN
  #define E1_CS_PIN        P1_01
#endif

#define TEMP_1_PIN         P0_23_A0   // A2 (T2) - (69) - TEMP_1_PIN
#define TEMP_BED_PIN       P0_25_A2   // A0 (T0) - (67) - TEMP_BED_PIN

//
// Software SPI pins for TMC2130 stepper drivers
//
#if ENABLED(TMC_USE_SW_SPI)
  #ifndef TMC_SW_MOSI
    #define TMC_SW_MOSI    P1_17
  #endif
  #ifndef TMC_SW_MISO
    #define TMC_SW_MISO    P0_05
  #endif
  #ifndef TMC_SW_SCK
    #define TMC_SW_SCK     P0_04
  #endif
#endif

#if HAS_TMC220x
  /**
   * TMC2208/TMC2209 stepper drivers
   *
   * Hardware serial communication ports.
   * If undefined software serial is used according to the pins below
   */
  //#define X_HARDWARE_SERIAL  Serial
  //#define X2_HARDWARE_SERIAL Serial1
  //#define Y_HARDWARE_SERIAL  Serial1
  //#define Y2_HARDWARE_SERIAL Serial1
  //#define Z_HARDWARE_SERIAL  Serial1
  //#define Z2_HARDWARE_SERIAL Serial1
  //#define E0_HARDWARE_SERIAL Serial1
  //#define E1_HARDWARE_SERIAL Serial1
  //#define E2_HARDWARE_SERIAL Serial1
  //#define E3_HARDWARE_SERIAL Serial1
  //#define E4_HARDWARE_SERIAL Serial1

  //
  // Software serial
  //
  #define X_SERIAL_TX_PIN  P1_10
  #define X_SERIAL_RX_PIN  P1_10

  #define Y_SERIAL_TX_PIN  P1_09
  #define Y_SERIAL_RX_PIN  P1_09

  #define Z_SERIAL_TX_PIN  P1_08
  #define Z_SERIAL_RX_PIN  P1_08

  #define E0_SERIAL_TX_PIN P1_04
  #define E0_SERIAL_RX_PIN P1_04

  #define E1_SERIAL_TX_PIN P1_01
  #define E1_SERIAL_RX_PIN P1_01

  #define Z2_SERIAL_TX_PIN P1_01
  #define Z2_SERIAL_RX_PIN P1_01

  // Reduce baud rate to improve software serial reliability
  #define TMC_BAUD_RATE 19200
#endif

//
// SD Connection
//
#if SD_CONNECTION_IS(LCD)
  #define SS_PIN           P0_16
#endif
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

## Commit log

2020-03-18 Initial Firmware
    [Configuration.h, Configuration_adv.h]
2020-03-18 Add ready to use firmware.bin
    [Configuration.h]
2020-03-18 Add simply3d profile for pla with layer 0.2mm and 0.1mm
2020-03-21 Add firmware 2.0.5.1 and Simplify 3D Profile for PLA 0.1mm
    [Configuration.h, Configuration_adv.h]
2020-03-21 ๊Update readme
2020-03-22 Add profile for PETG 0.2mm
    Use for functional parts
2020-04-11 Create Bill Of Material
2020-04-11 Add bill of material and update firmware for Bear SKR PINDA 2.0.5.3
    [Configuration.h, Configuration_adv.h]
2020-04-12 Add printed parts
    [Anchor_SKR_Bear_Short_1.stl, Bear_MK3_Body.stl, Bear_MK3_Cover.stl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]
2020-04-12 Add TFT35 Cover
    [cover_lcd_skr.stl, sd_bracket.stl, usb_bracket.stl]
2020-04-13 Add Mean Well LRS-350 PSU Case
    [bottom.stl, case.stl, psu_upper_mount_mean_well_lrs_350.stl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]
2020-04-14 Add TFT35 V3 Firmware Source Code with Custom Menu by Narasak Mansurang
    [Configuration.h]
2020-04-17 Add firmware for 0.9 on X, Y and E
    [Configuration.h, Configuration_adv.h]
2020-04-18 Update motor current for 0.9 Degree Stepper
    [Configuration_adv.h]

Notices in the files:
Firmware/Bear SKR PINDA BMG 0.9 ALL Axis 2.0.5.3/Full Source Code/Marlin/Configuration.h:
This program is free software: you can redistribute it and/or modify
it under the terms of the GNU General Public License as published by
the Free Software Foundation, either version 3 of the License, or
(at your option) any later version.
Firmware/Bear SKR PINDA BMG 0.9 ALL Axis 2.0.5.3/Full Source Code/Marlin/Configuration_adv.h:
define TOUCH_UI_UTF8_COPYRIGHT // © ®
